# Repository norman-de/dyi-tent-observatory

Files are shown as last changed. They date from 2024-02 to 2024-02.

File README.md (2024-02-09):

# dyi-tent-observatory

Lightweight diy tent observatory for my 6" astro telescope

tent-observatory
tent-observatory
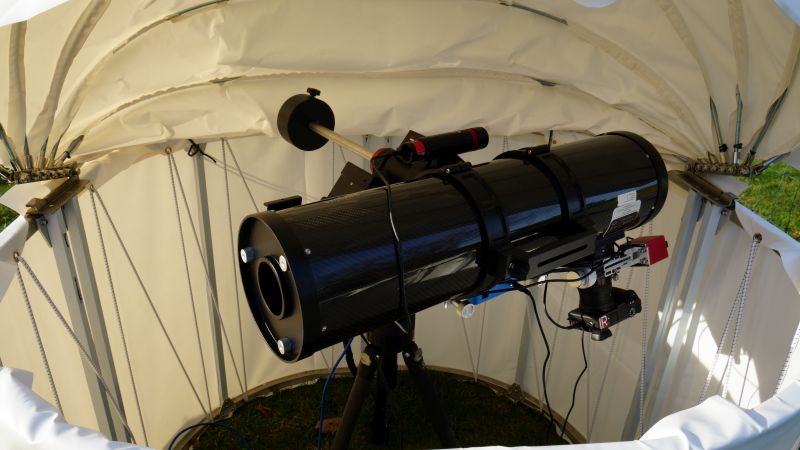
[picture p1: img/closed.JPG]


## Beschreibung

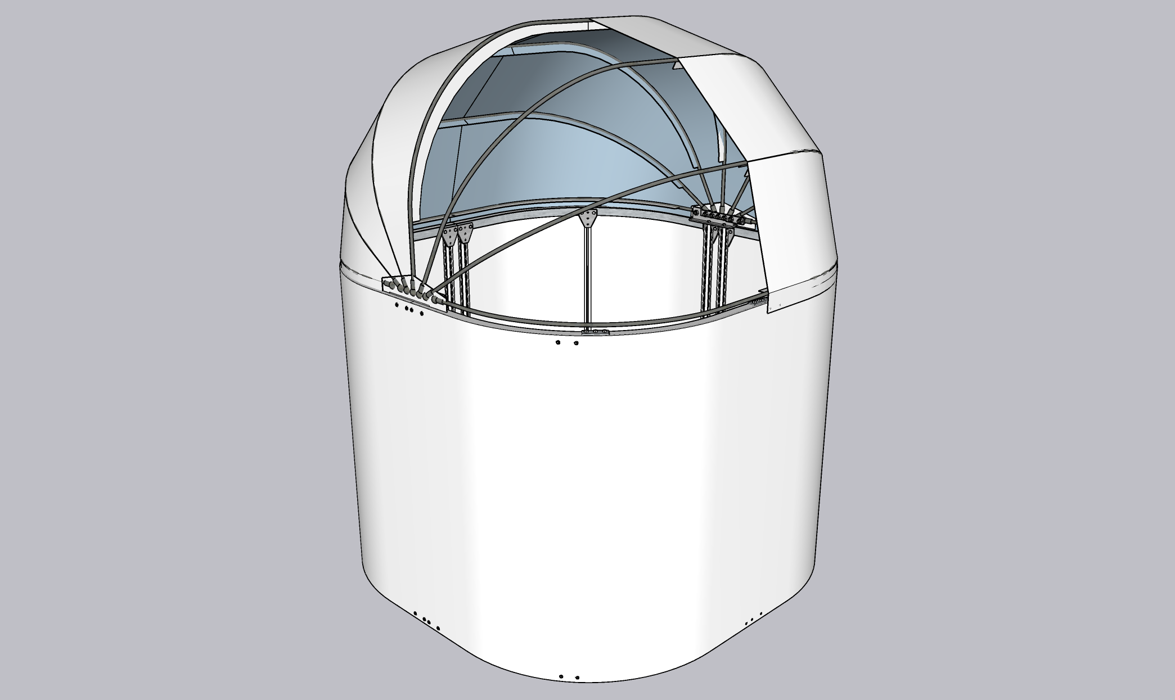
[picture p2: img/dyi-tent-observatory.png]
tent-observatory

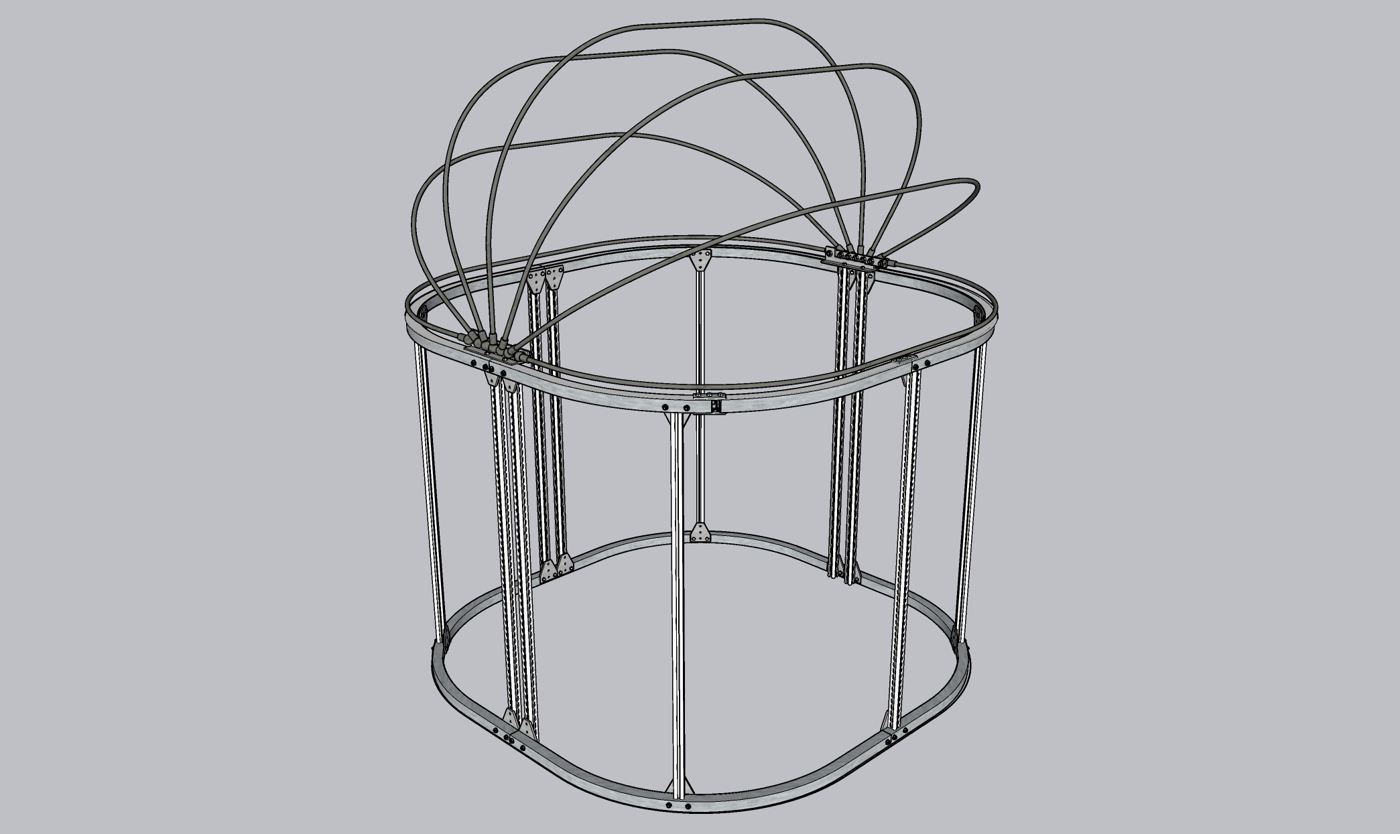
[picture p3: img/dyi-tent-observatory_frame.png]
tent-observatory


Ein robustes Igluzelt, das leicht selbst gebaut werden kann und wind- und wasserdicht ist. Die Plane für das Faltdach wird selbst genäht, wofür eine robuste Nähmaschine erforderlich ist. Der Vorteil des Nähens (im Gegensatz zum Schweißen oder Kleben) ist, dass die Schlaufen für die Stützstangen leicht herzustellen sind. Die Rundungen der Grundform aus 25 mm Vierkantstahl wurden mit einer Biegemaschine hergestellt, aber natürlich sind auch eckige Formen möglich. Der Klappmechanismus des Daches ist ein Kompromiss, er ist einfach zu bauen (abgesehen vom Bohren der Löcher in den 5 mm Stahl) und ermöglicht das vollständige Absenken des Daches hinter den Rahmenhorizont. Es ist jedoch nicht von Vorteil, wenn das Öffnen und Schließen automatisiert werden soll.

Details der Konstruktion können der SketchUp-Datei entnommen werden.

## Basis

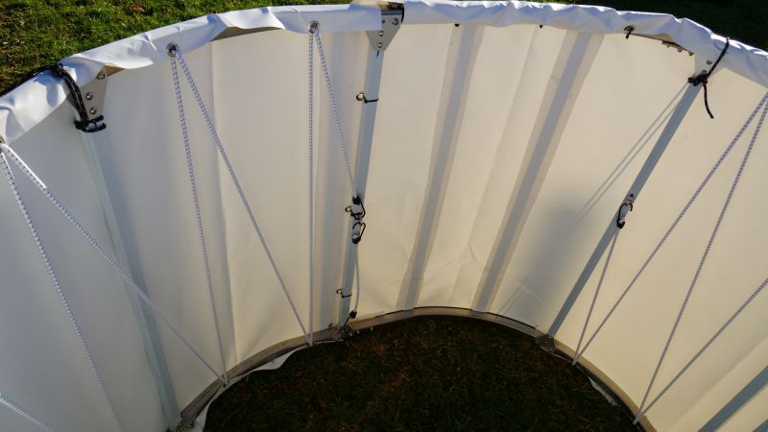
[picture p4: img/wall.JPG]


Damit das Dach später windschnittig ist, habe ich eine abgerundete Form gewählt, ganz rund konnte ich es nicht bauen, da ich 1m Vierkantprofile hatte und die Biegemaschine nicht bis zum Rand biegen kann. Die Vierkantprofile sind mit kurzen 20mm Vierkantprofilen ineinander gesteckt. Als Stützstreben verwende ich Aluprofile mit Nut, das ist stabil und die Befestigungen sind variabel. Die LKW-Plane wird am Ende wie bei einer Trommel darüber gespannt.

## Tür

tent-observatory

Die Tür habe ich improvisiert, sie ist nur aus den oberen Vierkantprofilen ausgeschnitten. In die Plane habe ich Magnetstreifen zum Verschließen eingeklebt und unten einen Druckknopf, es hat sich herausgestellt das die Plane der Tür unten durch den Wind eingedrückt wird, deshalb habe ich noch 2 Alu-Flachprofile eingeklebt um die Plane steifer zu machen.

## Klappgelenk

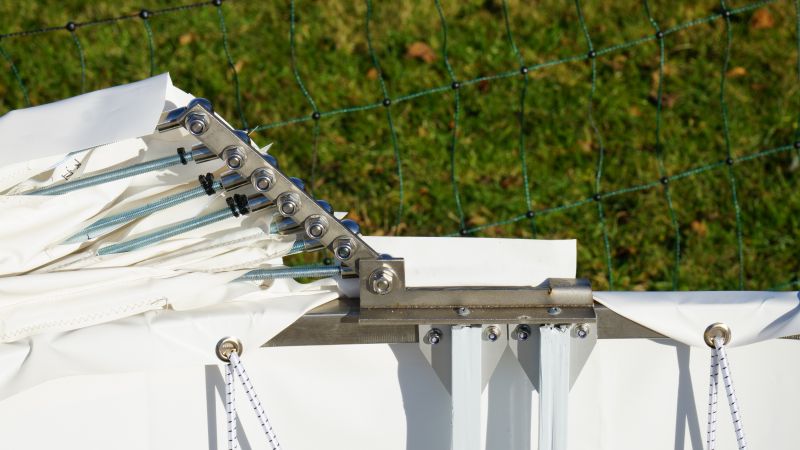
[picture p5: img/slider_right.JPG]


Das Klappgelenk habe ich aus einem Stück Flachstahl und einem T-Profil gebaut. Dazu wird das T-Profil mit der Flex angepasst und ein Stück für die Auflage mit dem Hammer gebogen. Als Verbindung zu den Gewindestangen habe ich Winkelgelenke für Gasfedern in der Stärke der Gewindestangen genommen, was das Ganze sehr einfach macht. Die Löcher müssen weit genug auseinander sein, damit sich die Stangen bewegen können.

## Dach

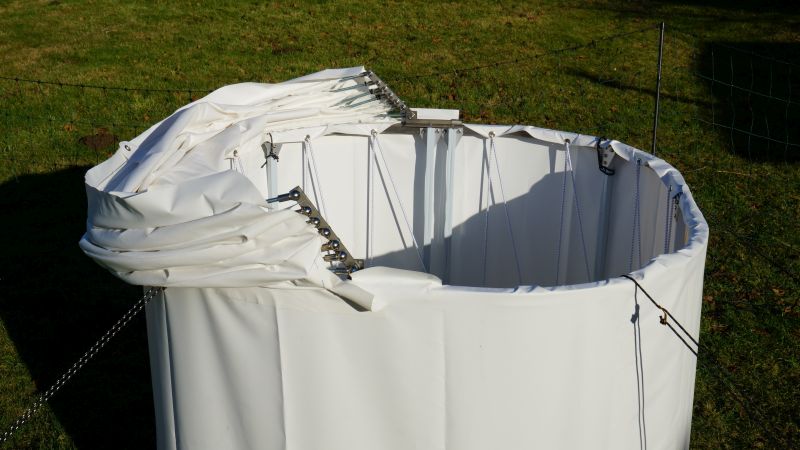
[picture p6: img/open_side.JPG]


Die Winkel der Dachträger sind so berechnet, dass ihr höchster Punkt dort liegt, wo er bei sternförmiger Anordnung der Stützen liegen würde. Da sie jedoch nicht den gleichen Ausgangspunkt haben, sind die Träger unterschiedlich lang und in verschiedenen Winkeln angeordnet. Das Schnittmuster für das Dach habe ich erstellt, indem ich die 3D-Oberfläche des Modells mit dem SketchUp-Plugin "Unwrap and Flutter Faces" zu einer ebenen Fläche verformt habe. Das PDF "Teil 1" zeigt also die Fläche zwischen dem Mittelpfosten und der nächsten Strebe von außen und muss zum Nähen einen entsprechenden Nähzugabe erhalten.

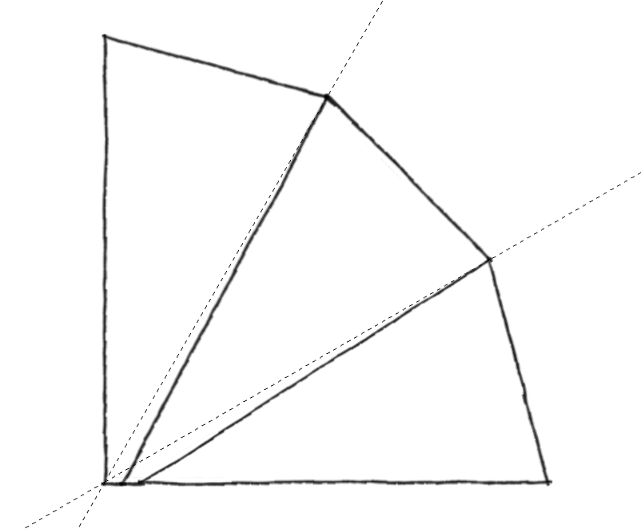
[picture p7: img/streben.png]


## Teileliste

### Nützliches Werkzeug

* Flex / Akkuschrauber / ...
* BOKA Biegemaschine TR-40
* Schneidpaste zum Bohren
* Sabacontact 70T PVC Kleber für Planen
* Leder-Nadeln Nadeldicke 120/19
* Teflonfuß/Gleitfuß Nähfuss
* CRAFTUS® Profi Ösenzange
* Sxdluzi Locher 10mm zum Vorlochen
* LIQUI MOLY Schraubensicherung
* Aussen-Entgrater für Ø 3-19 mm für die Gewindestangen

### Material

* 7 x Gewindestange M8 Länge 2m
* 14 x M8 Winkelgelenk 304 V2A (30mm)
* 1x T-Profil V2A 40 x 40 x 4 mm, 1m
* 1x Flachstahl V2A 20 x 5 mm, 0,5m
* 1x PVC-Plane 450g/m² - 3 m x 5 m
* 8 x Vierkantrohr V2A 25 x 25 x 2 mm, 1m
* 1 x Vierkantrohr V2A 20 x 20 x 2 mm, 1m
* 6 x Aluprofil 20x20 Nut6 Typ B, 6x2m
* 22 x Eckhalterungsverbindungsplatte T-Form
* 20m x Expanderseil 6mm
* 2 X Ringösenschrauben mit Außengewind
* 2 x Spiralhaken für ø 6mm Expanderseile
* M5x35 V2A Schrauben / Muttern
* A+B Magnetband2m für die Tür
* AMANN Nähgarn Serabond 30

**Summe:** ca. 1000€ (Inkl. 240€ Biegemaschien)

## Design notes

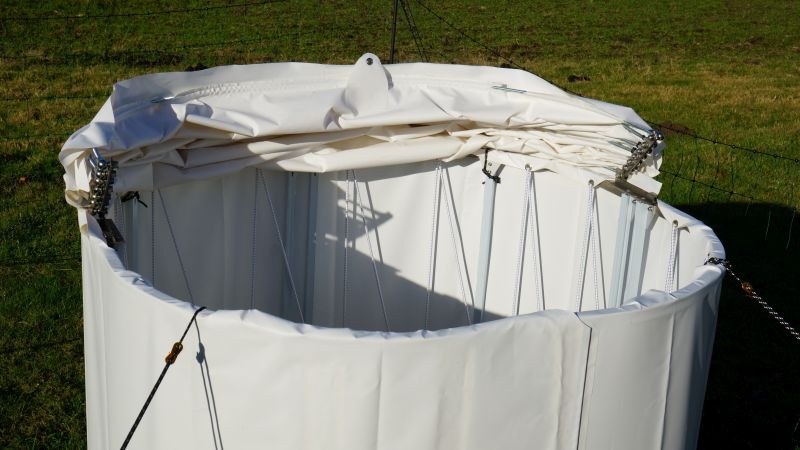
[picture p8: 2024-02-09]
img/open_front.JPG

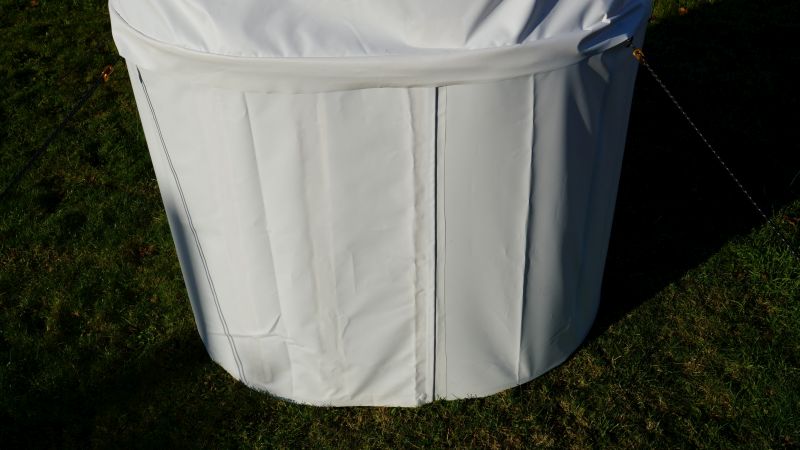
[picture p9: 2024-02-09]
img/door_outside.JPG

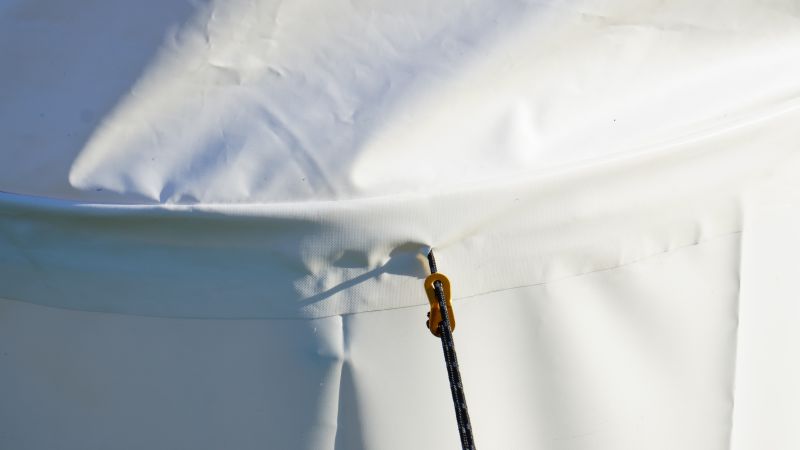
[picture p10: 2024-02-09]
img/hook.JPG

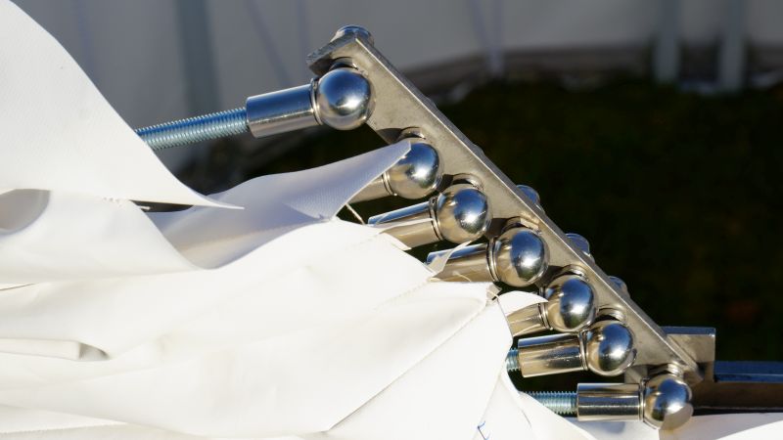
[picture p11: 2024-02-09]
img/slider_left.JPG

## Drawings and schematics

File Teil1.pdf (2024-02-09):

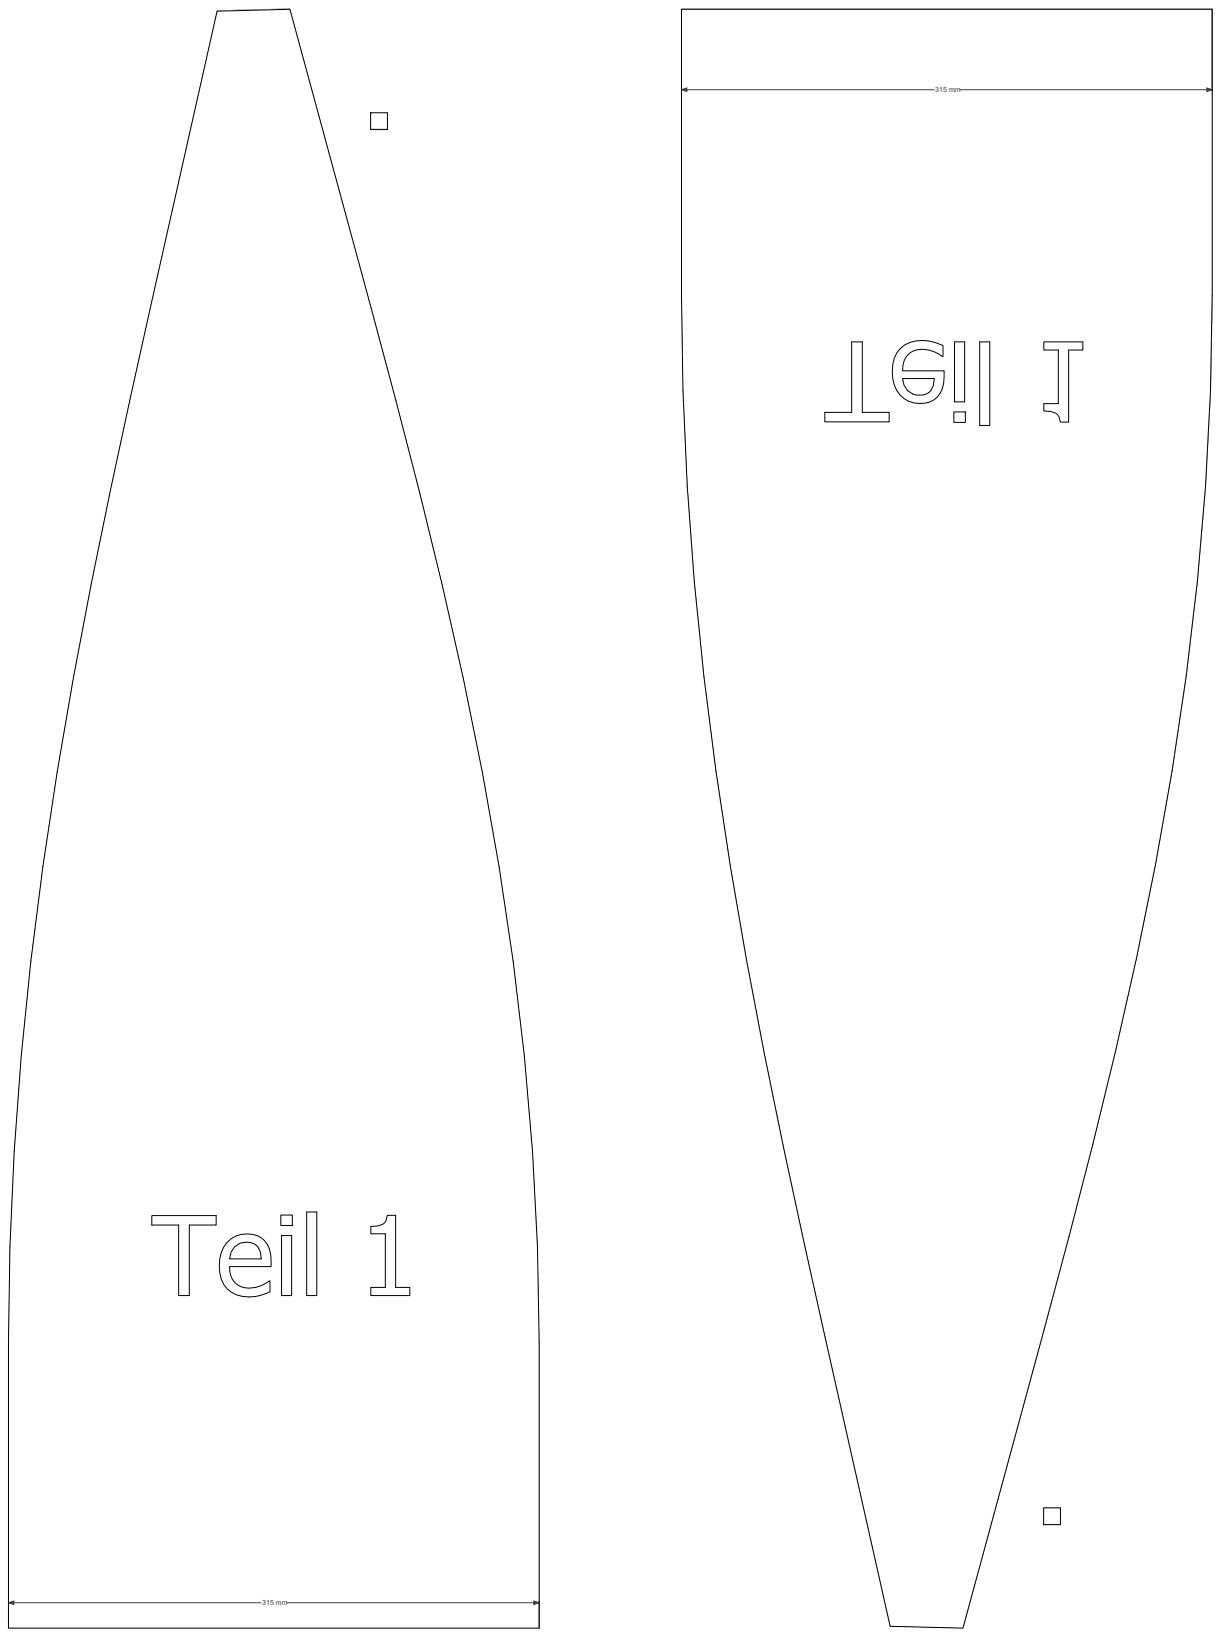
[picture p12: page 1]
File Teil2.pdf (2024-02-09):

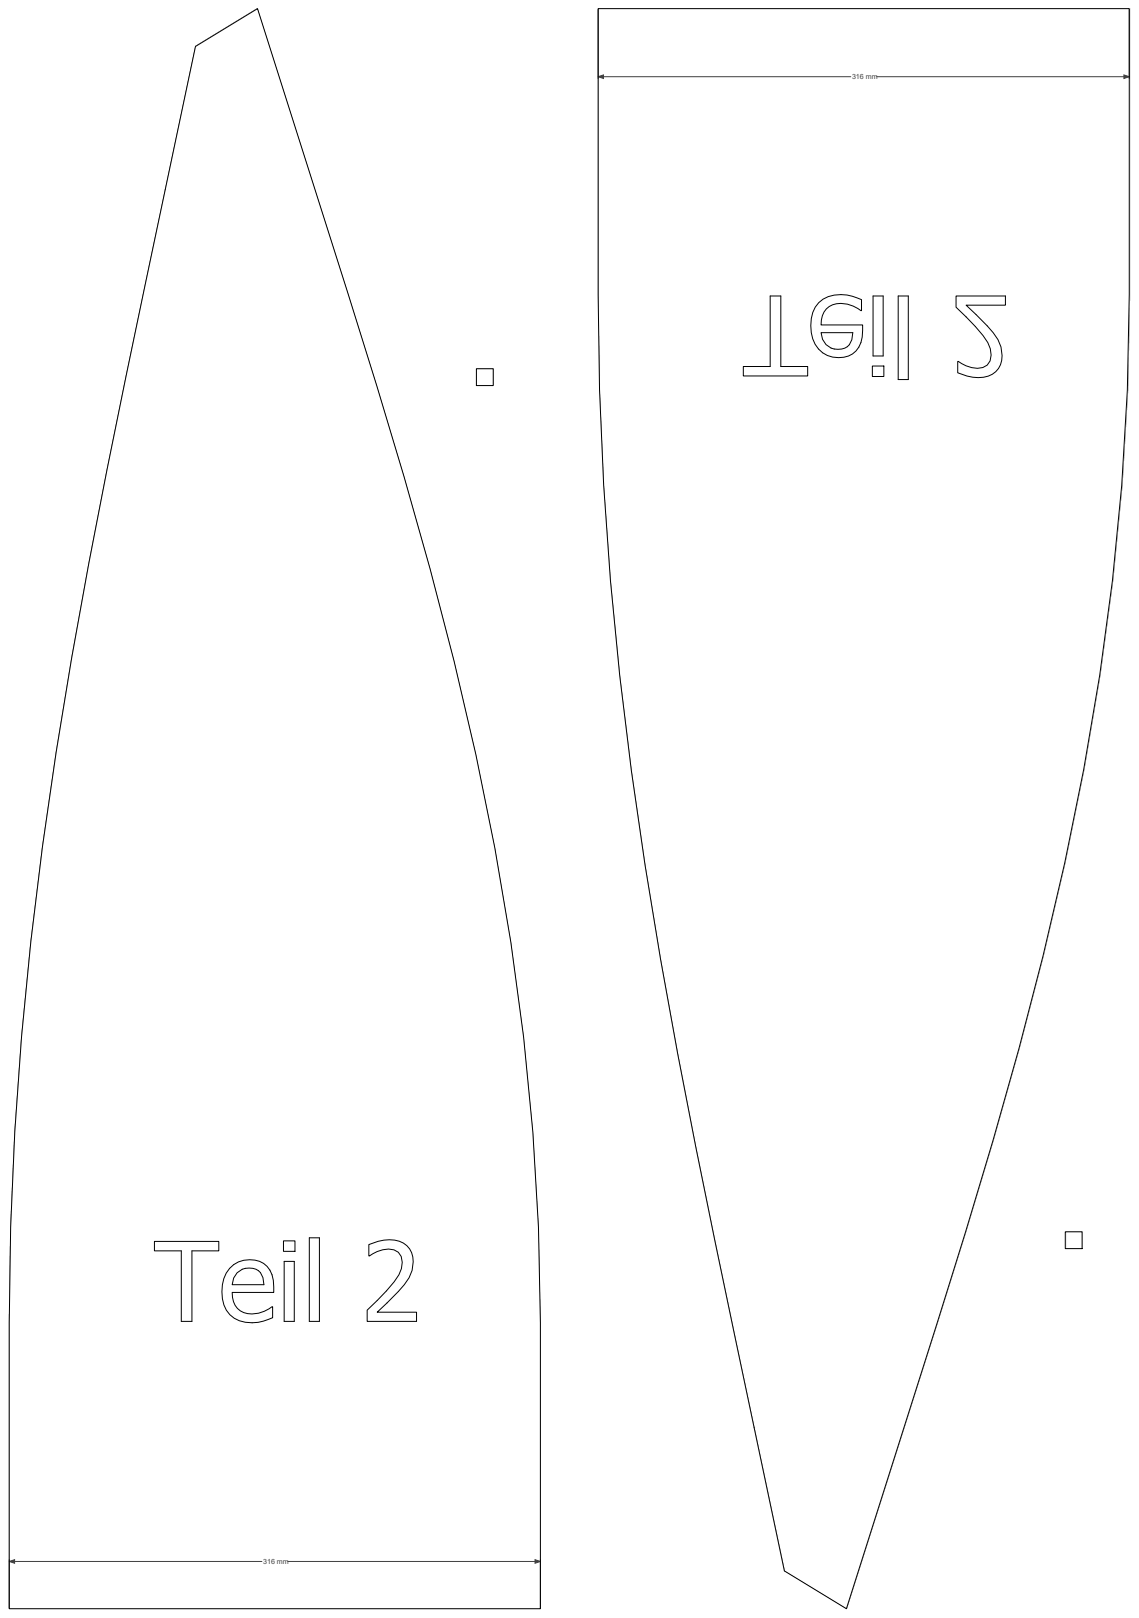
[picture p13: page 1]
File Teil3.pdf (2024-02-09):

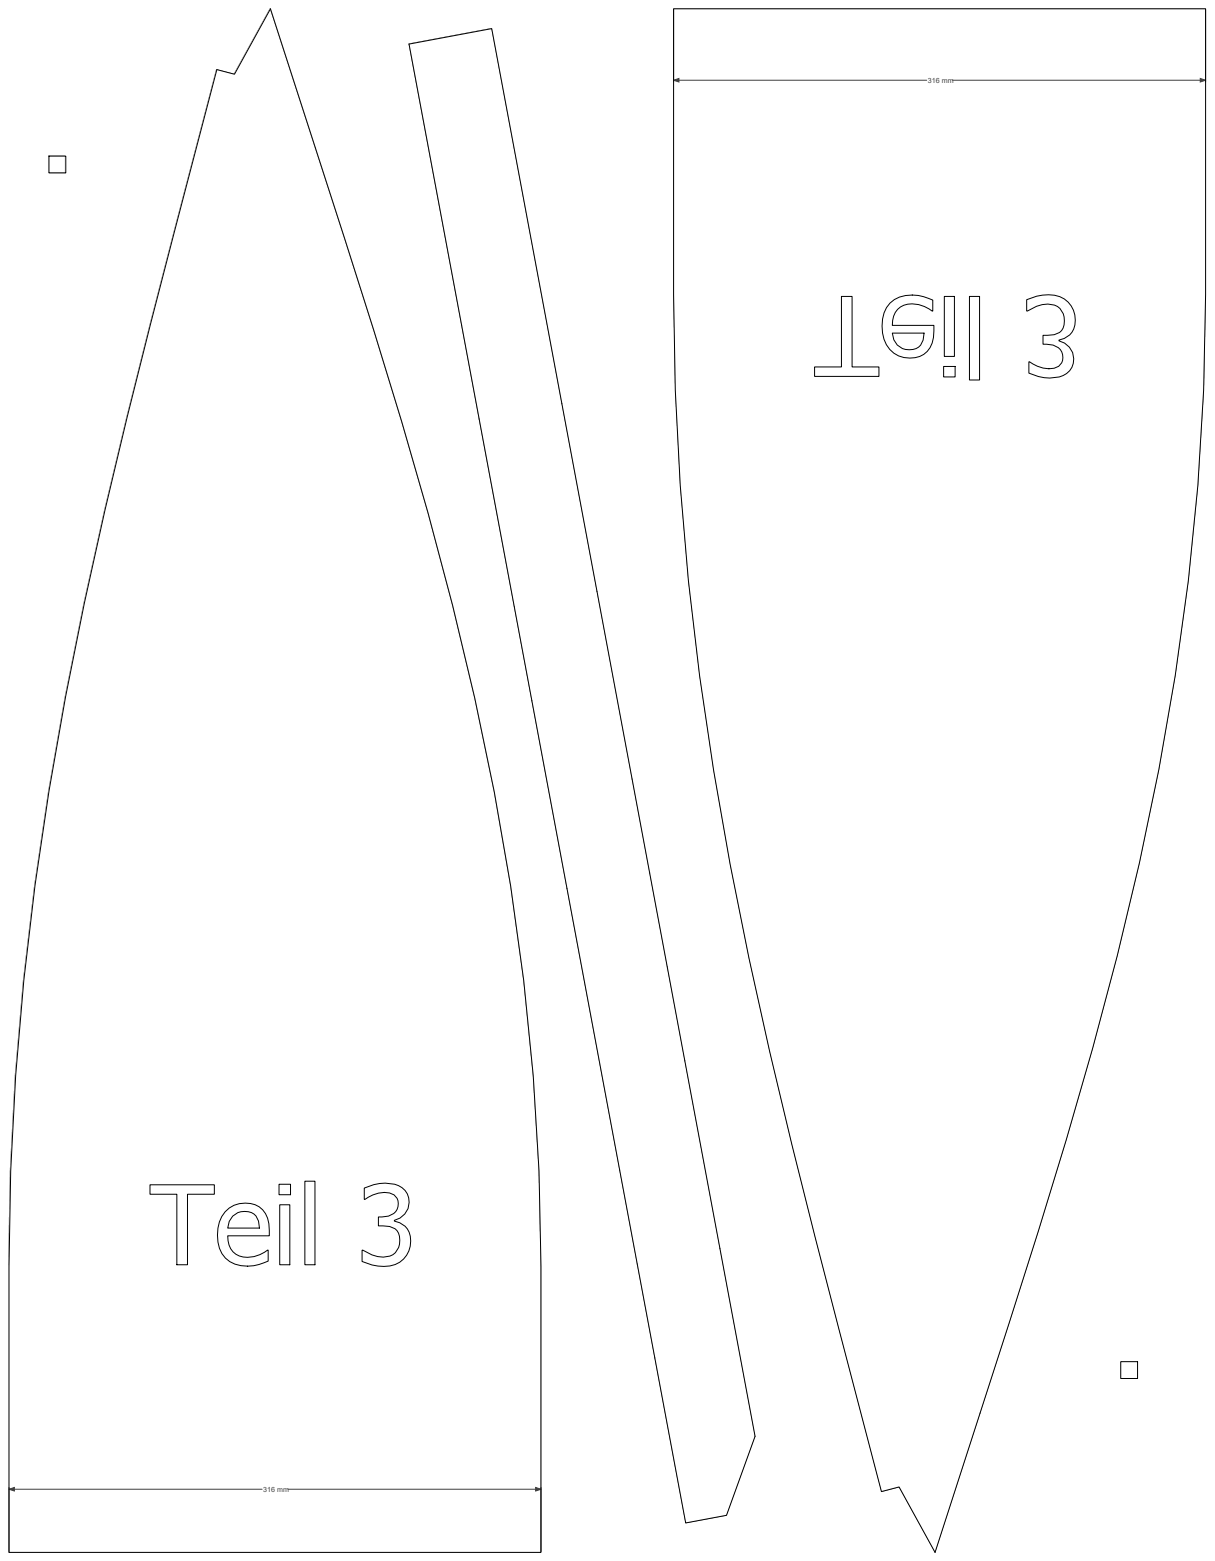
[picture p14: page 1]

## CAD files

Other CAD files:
dyi-tent-observatory.skp
